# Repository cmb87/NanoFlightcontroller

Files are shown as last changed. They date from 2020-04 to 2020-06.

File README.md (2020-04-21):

# Generic Arduino Based Flightcontroller

## Code
There are two versions:

## MultiWii based FC code
(see https://github.com/multiwii/multiwii-firmware.git for more details). 

### Compass module
Some modifications of the original code were necessary for the compass module (QMC5883L) and are described here:
https://forum.arduino.cc/index.php?topic=556590.0

0.) Navigate to config.h add the line somewhere behind /* I2C magnetometer */:

        #define QMC5883
        
1.) Navigate to sensors.cpp add following somewhere behind the last #endif statement at the magnetometer section:

        // ************************************************************************************************************
        // I2C Compass QMC5883L
        // ************************************************************************************************************
        // I2C adress: 0x0D (7bit)
        // ************************************************************************************************************
        #if defined(QMC5883)

        #define MAG_ADDRESS 0x0D
        #define MAG_DATA_REGISTER 0x00

        //REG CONTROL

        #define MAG_CTRL_REG1 0x09
        #define QMC_MODE 0xC1 // 11 00 00 01OSR=64(11); Range=2G(00); ODR=10Hz(00); MODE=Cont(01)
        #define MAG_CTRL_REG2 0x0A

        void Mag_init() {
          i2c_writeReg(MAG_ADDRESS,0x0B,0x01);
          i2c_writeReg(MAG_ADDRESS,MAG_CTRL_REG1,QMC_MODE);
        }

        static void getADC() {
          i2c_getSixRawADC(MAG_ADDRESS,MAG_DATA_REGISTER);
          MAG_ORIENTATION( ((rawADC[1]<<8) | rawADC[0]) ,
                           ((rawADC[3]<<8) | rawADC[2]) ,
                           ((rawADC[5]<<8) | rawADC[4]) );
        }

        #if !defined(MPU6050_I2C_AUX_MASTER)
        static void Device_Mag_getADC() {
          getADC();
        }
        #endif
        #endif

Now we need to add the QMC to the MPU6050 I2C Master & Slave functionality:

Search for this comment in sensors.cpp:

        //The MAG acquisition function must be replaced because we now talk to the MPU device

Add following lines inside static void Device_Mag_getADC(){} after i2c_getSixRawADC(MPU6050_ADDRESS, 0x49);:

        #if defined(QMC5883)
                MAG_ORIENTATION( ((rawADC[1]<<8) | rawADC[0]) ,
                                 ((rawADC[3]<<8) | rawADC[2]) ,
                                 ((rawADC[5]<<8) | rawADC[4]) );
              #endif
              
Navigate to def.h search for the MAG 1 definition "#if" clause - add "|| defined(QMC5883)" - like this:

        #if defined(HMC5883) || defined(HMC5843) || defined(AK8975) || defined(MAG3110) || defined(QMC5883)
          #define MAG 1
        #else
          #define MAG 0
        #endif
              
The original HMC5883 Code has lots of more lines because of some ominous bias and gain settings - the QMC5883 lacks those registers - Unfortunately I don't have any knowledge about this and its benefits and no time to get into it. The data provided by the sensor seems to be reliable.

### Setup
Due to the construction of the flight controller the following settings were necessary:
            
          MINTHROTTLE = 1150
          # ==============================================
          # MPU Setup 
          # ==============================================
          # Roll and Yaw inverted
          #define ACC_ORIENTATION(X, Y, Z) {imu.accADC[ROLL] =  -X; imu.accADC[PITCH] =  -Y; imu.accADC[YAW] = Z;}
          #define GYRO_ORIENTATION(X, Y, Z) {imu.gyroADC[ROLL] = -X; imu.gyroADC[PITCH] = -Y; imu.gyroADC[YAW] = Z;}
          
          # ==============================================
          # Inverted Pitch ... let's see ===> Not a good idea ... Create oscillations!
          #define ACC_ORIENTATION(X, Y, Z) {imu.accADC[ROLL] =  X; imu.accADC[PITCH] =  Y; imu.accADC[YAW] = -Z;}
          #define GYRO_ORIENTATION(X, Y, Z) {imu.gyroADC[ROLL] = -X; imu.gyroADC[PITCH] = Y; imu.gyroADC[YAW] = -Z;}

          # ==============================================
          WORKING!!!!
          # Roll and Yaw inverted ==> Stabilize around roll axis! Roll appears inverted in MultiwiiConf!!!
          #define ACC_ORIENTATION(X, Y, Z) {imu.accADC[ROLL] =  X; imu.accADC[PITCH] =  -Y; imu.accADC[YAW] = -Z;}
          #define GYRO_ORIENTATION(X, Y, Z) {imu.gyroADC[ROLL] = -X; imu.gyroADC[PITCH] = -Y; imu.gyroADC[YAW] = -Z;}
          # PID Coeff; Roll; 4.1, 0.004,9 Pitch:1.6, 0.003,4 Yaw: 1.6, 0.003, 2
          
          # ==============================================
          # MPU + Compass
          # ==============================================
          WORKING!!!! Works perfectly with 
          #define YAW_DIRECTION -1
          #define ACC_ORIENTATION(X, Y, Z) {imu.accADC[ROLL] =  X; imu.accADC[PITCH] =  -Y; imu.accADC[YAW] = -Z;}
          #define GYRO_ORIENTATION(X, Y, Z) {imu.gyroADC[ROLL] = -X; imu.gyroADC[PITCH] = -Y; imu.gyroADC[YAW] = -Z;}
          #define FORCE_MAG_ORIENTATION(X, Y, Z)  {imu.magADC[ROLL]  =   -X; imu.magADC[PITCH]  =  -Y; imu.magADC[YAW]  = -Z;}

### ESC Calibration
Dont forget the ESC calibration in config.h!

### Custom Arduino based FC code
Inspired by http://www.electronoobs.com

## PCB
Created with Fritzing and Flatcam.

# Issues
Some issues encountered during the construction phase.

## Vibrations
Has a very intensive impact on PID controller resulting in twitches and an in general "nervous" behaviour of the quad. In order to mitigate there are three ways:

    1.) Reduce vibrations by accurately balancing propellers
    2.) Increase damping of the flight controller module
    3.) In MultiWii: Reduce low pass filter to e.g. 42hz for gyro and activate moving average filter (with default settings). Search for LPF in config.h

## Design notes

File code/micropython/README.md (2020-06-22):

https://github.com/tuupola/micropython-mpu9250

# By default the library returns 3-tuple of X, Y, Z axis values for either acceleration, gyroscope and magnetometer ie compass. Default units are m/s^2, rad/s, uT and °C. It is possible to also get acceleration values in g and gyro values deg/s. See the example below. Note that both the MPU6500 and the AK8963 drivers are available as separate classes. MPU9250 is actually a composite of those two.

import utime
from machine import I2C, Pin
from mpu9250 import MPU9250

i2c = I2C(scl=Pin(22), sda=Pin(21))
sensor = MPU9250(i2c)

print("MPU9250 id: " + hex(sensor.whoami))

while True:
    print(sensor.acceleration)
    print(sensor.gyro)
    print(sensor.magnetic)
    print(sensor.temperature)

    utime.sleep_ms(1000)

# More realistic example usage with timer. If you get OSError: 26 or i2c driver install error after soft reboot do a hard reboot.

import utime
from machine import I2C, Pin
from mpu9250 import MPU9250
from mpu6500 import MPU6500, SF_G, SF_DEG_S

i2c = I2C(scl=Pin(22), sda=Pin(21))
mpu6500 = MPU6500(i2c, accel_sf=SF_G, gyro_sf=SF_DEG_S)
sensor = MPU9250(i2c, mpu6500=mpu6500)

print("MPU9250 id: " + hex(sensor.whoami))

while True:
    print(sensor.acceleration)
    print(sensor.gyro)
    print(sensor.magnetic)
    print(sensor.temperature)

    utime.sleep_ms(1000)

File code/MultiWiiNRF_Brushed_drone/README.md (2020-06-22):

/*  From iforced2D, changed by ELECTRONOOBS 02/03/2018
 *  This is the code used for a brushed drone. Motors are conencted to D3, D5, D6 adn D9
 *  NRF24 is connected to D13, D12, D11, D8 and D7
 *  IMU is connected to A4 and A5
 *  Check the tutorial here: http://www.electronoobs.com/eng_arduino_tut23.php
 *  And the video here: https://www.youtube.com/watch?v=uZKINPm3P9E
 *  
 * 
 * Go to NRF24_RX if you want to change CE adn CSN pins and the received bytes
 * Go to config.c to cahnge drone configuration
 * Go to output.cpp to cahnge the output PWM signal
 * 
 * 
 * 
 * 
 * 
 * 
 * 
 * 
 * 
 * Welcome to MultiWii.
 *
 * If you see this message, chances are you are using the Arduino IDE. That is ok.
 * To get the MultiWii program configured for your copter, you must switch to the tab named 'config.h'.
 * Maybe that tab is not visible in the list at the top, then you must use the drop down list at the right
 * to access that tab. In that tab you must enable your baord or sensors and optionally various features.
 * For more info go to http://www.multiwii.com/wiki/index.php?title=Main_Page
 *
 * Have fun, and do not forget MultiWii is made possible and brought to you under the GPL License.
 *
 */

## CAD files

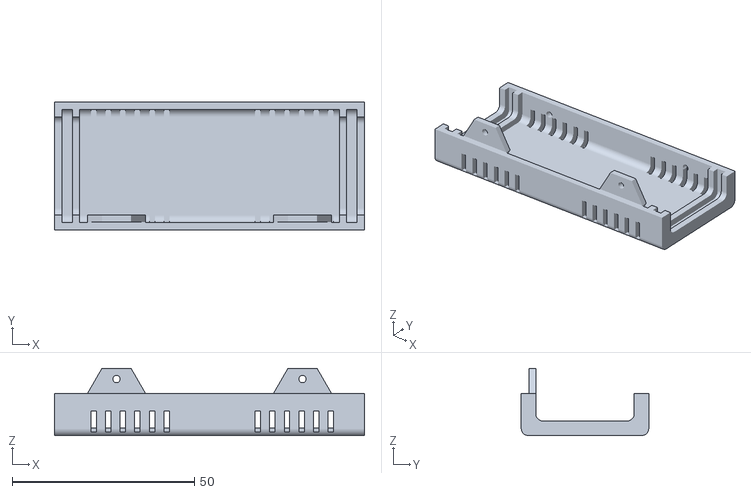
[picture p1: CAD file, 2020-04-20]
casing/bottom.stl
85.0 x 35.0 x 18.4

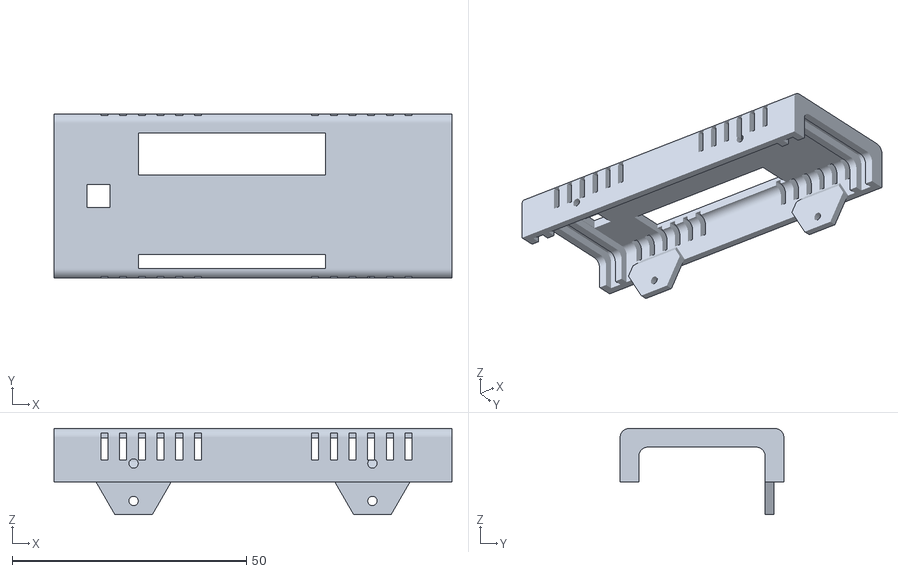
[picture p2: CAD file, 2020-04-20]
casing/top.stl
85.0 x 35.0 x 18.4

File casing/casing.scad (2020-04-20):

/*//////////////////////////////////////////////////////////////////
              -    FB Aka Heartman/Hearty 2016     -                   
              -   http://heartygfx.blogspot.com    -                  
              -       OpenScad Parametric Box      -                     
              -         CC BY-NC 3.0 License       -                      
////////////////////////////////////////////////////////////////////                                                                                                             
12/02/2016 - Fixed minor bug 
28/02/2016 - Added holes ventilation option                    
09/03/2016 - Added PCB feet support, fixed the shell artefact on export mode. 

*/////////////////////////// - Info - //////////////////////////////

// All coordinates are starting as integrated circuit pins.
// From the top view :

//   CoordD           <---       CoordC
//                                 ^
//                                 ^
//                                 ^
//   CoordA           --->       CoordB


////////////////////////////////////////////////////////////////////


////////// - Paramètres de la boite - Box parameters - /////////////

/* [Box dimensions] */
// - Longueur - Length  
  Length        = 75+14-4;       
// - Largeur - Width
  Width         = 31+4;                     
// - Hauteur - Height  
  Height        = 23;  
// - Epaisseur - Wall thickness  
  Thick         = 2;//[2:5]  
  
/* [Box options] */
// Pieds PCB - PCB feet (x4) 
  PCBFeet       = 0;// [0:No, 1:Yes]
// - Decorations to ventilation holes
  Vent          = 1;// [0:No, 1:Yes]
// - Decoration-Holes width (in mm)
  Vent_width    = 1.5;   
// - Text you want
  txt           = "cmb87";           
// - Font size  
  TxtSize       = 3;                 
// - Font  
  Police        ="Arial Black"; 
// - Diamètre Coin arrondi - Filet diameter  
  Filet         = 2;//[0.1:12] 
// - lissage de l'arrondi - Filet smoothness  
  Resolution    = 50;//[1:100] 
// - Tolérance - Tolerance (Panel/rails gap)
  m             = 0.9;
  
/* [PCB_Feet--the_board_will_not_be_exported) ] */
//All dimensions are from the center foot axis
// - Coin bas gauche - Low left corner X position
PCBPosX         = 7;
// - Coin bas gauche - Low left corner Y position
PCBPosY         = 6;
// - Longueur PCB - PCB Length
PCBLength       = 70;
// - Largeur PCB - PCB Width
PCBWidth        = 50;
// - Heuteur pied - Feet height
FootHeight      = 10;
// - Diamètre pied - Foot diameter
FootDia         = 8;
// - Diamètre trou - Hole diameter
FootHole        = 3;  
  

/* [STL element to export] */
//Coque haut - Top shell
  TShell        = 1;// [0:No, 1:Yes]
//Coque bas- Bottom shell
  BShell        = 0;// [0:No, 1:Yes]
//Panneau arrière - Back panel  
  BPanel        = 0;// [0:No, 1:Yes]
//Panneau avant - Front panel
  FPanel        = 0;// [0:No, 1:Yes]
//Texte façade - Front text
  Text          = 0;// [0:No, 1:Yes]


  
/* [Hidden] */
// - Couleur coque - Shell color  
Couleur1        = "Orange";       
// - Couleur panneaux - Panels color    
Couleur2        = "OrangeRed";    
// Thick X 2 - making decorations thicker if it is a vent to make sure they go through shell
Dec_Thick       = Vent ? Thick*2 : Thick; 
// - Depth decoration
Dec_size        = Vent ? Thick*2 : 0.8;

//////////////////// Oversize PCB limitation -Actually disabled - ////////////////////
//PCBL= PCBLength+PCBPosX>Length-(Thick*2+7) ? Length-(Thick*3+20+PCBPosX) : PCBLength;
//PCBW= PCBWidth+PCBPosY>Width-(Thick*2+10) ? Width-(Thick*2+12+PCBPosY) : PCBWidth;
PCBL=PCBLength;
PCBW=PCBWidth;
//echo (" PCBWidth = ",PCBW);

//translate([7,2.5,6])cube([75,30,2]);

/////////// - Boitier générique bord arrondis - Generic Fileted box - //////////

module RoundBox($a=Length, $b=Width, $c=Height){// Cube bords arrondis
                    $fn=Resolution;            
                    translate([0,Filet,Filet]){  
                    minkowski (){                                              
                        cube ([$a-(Length/2),$b-(2*Filet),$c-(2*Filet)], center = false);
                        rotate([0,90,0]){    
                        cylinder(r=Filet,h=Length/2, center = false);
                            } 
                        }
                    }
                }// End of RoundBox Module

      
////////////////////////////////// - Module Coque/Shell - //////////////////////////////////         

module Coque(){//Coque - Shell  
    Thick = Thick*2;  
    difference(){    
        difference(){//sides decoration
            union(){    
                     difference() {//soustraction de la forme centrale - Substraction Fileted box
                      
                        difference(){//soustraction cube median - Median cube slicer
                            union() {//union               
                            difference(){//Coque    
                                RoundBox();
                                translate([Thick/2,Thick/2,Thick/2]){     
                                        RoundBox($a=Length-Thick, $b=Width-Thick, $c=Height-Thick);
                                        }
                                        }//Fin diff Coque                            
                                difference(){//largeur Rails        
                                     translate([Thick+m,Thick/2,Thick/2]){// Rails
                                          RoundBox($a=Length-((2*Thick)+(2*m)), $b=Width-Thick, $c=Height-(Thick*2));
                                                          }//fin Rails
                                     translate([((Thick+m/2)*1.55),Thick/2,Thick/2+0.1]){ // +0.1 added to avoid the artefact
                                          RoundBox($a=Length-((Thick*3)+2*m), $b=Width-Thick, $c=Height-Thick);
                                                    }           
                                                }//Fin largeur Rails
                                    }//Fin union                                   
                               translate([-Thick,-Thick,Height/2]){// Cube à soustraire
                                    cube ([Length+100, Width+100, Height], center=false);
                                            }                                            
                                      }//fin soustraction cube median - End Median cube slicer
                               translate([-Thick/2,Thick,Thick]){// Forme de soustraction centrale 
                                    RoundBox($a=Length+Thick, $b=Width-Thick*2, $c=Height-Thick);       
                                    }                          
                                }                                          


                difference(){// Fixation box legs
                    union(){
                        translate([3*Thick +5,Thick,Height/2]){
                            rotate([90,0,0]){
                                    $fn=6;
                                    cylinder(d=16,Thick/2);
                                    }   
                            }
                            
                       translate([Length-((3*Thick)+5),Thick,Height/2]){
                            rotate([90,0,0]){
                                    $fn=6;
                                    cylinder(d=16,Thick/2);
                                    }   
                            }

                        }
                            translate([4,Thick+Filet,Height/2-57]){   
                             rotate([45,0,0]){
                                   cube([Length,40,40]);    
                                  }
                           }
                           translate([0,-(Thick*1.46),Height/2]){
                                cube([Length,Thick*2,10]);
                           }
                    } //Fin fixation box legs
            }

        union(){// outbox sides decorations
            //if(Thick==1){Thick=2;
            for(i=[0:Thick:Length/4]){

                // Ventilation holes part code submitted by Ettie - Thanks ;) 
                    translate([10+i,-Dec_Thick+Dec_size,1]){
                    cube([Vent_width,Dec_Thick,Height/4]);
                    }
                    translate([(Length-10) - i,-Dec_Thick+Dec_size,1]){
                    cube([Vent_width,Dec_Thick,Height/4]);
                    }
                    translate([(Length-10) - i,Width-Dec_size,1]){
                    cube([Vent_width,Dec_Thick,Height/4]);
                    }
                    translate([10+i,Width-Dec_size,1]){
                    cube([Vent_width,Dec_Thick,Height/4]);
                    }
  
                
                    }// fin de for
               // }
                }//fin union decoration
            }//fin difference decoration
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

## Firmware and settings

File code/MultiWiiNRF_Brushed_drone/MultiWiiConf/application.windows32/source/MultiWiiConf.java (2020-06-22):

import processing.core.*; 
import processing.xml.*; 

import processing.serial.Serial; 
import controlP5.*; 
import processing.opengl.*; 
import java.lang.StringBuffer; 
import javax.swing.SwingUtilities; 
import javax.swing.JFileChooser; 
import javax.swing.filechooser.FileFilter; 
import javax.swing.JOptionPane; 
import java.util.*; 
import java.io.*; 

import java.applet.*; 
import java.awt.Dimension; 
import java.awt.Frame; 
import java.awt.event.MouseEvent; 
import java.awt.event.KeyEvent; 
import java.awt.event.FocusEvent; 
import java.awt.Image; 
import java.io.*; 
import java.net.*; 
import java.text.*; 
import java.util.*; 
import java.util.zip.*; 
import java.util.regex.*; 

public class MultiWiiConf extends PApplet {

 // serial library
 // controlP5 library
 
 // for efficient String concatemation
 // required for swing and EDT
 // Saving dialogue
 // for our configuration file filter "*.mwi"
 // for message dialogue

//Added For  Processing 2.0.x compabillity


//****************************

// TODO add new msp :  pid description with bound and scale

PrintWriter output;
BufferedReader reader;
String portnameFile="SerialPort.txt"; // Name of file for Autoconnect.
int GUI_BaudRate = 115200; // Default.
int SerialPort;
Serial g_serial;
ControlP5 controlP5;
Textlabel txtlblWhichcom,TxtInfoMotors1;
Textlabel txtlblRates,txtlblRev,TxtLeftW,TxtRightW,TxtRevW,TxtRevR,TxtRates,TxtRev,
          TxtMids,TxtMin,TxtMax,TxtSLeft,TxtSNick,TxtSRight,TxtInfo,TxtInfo1,TxtInfo2,
          TxtInfo3,TxtInfo4,TxtAux,Links;

ListBox commListbox,baudListbox;

static int CHECKBOXITEMS=0;
static int PIDITEMS=10;
int commListMax;
int tabHeight=20; // Extra height needed for Tabs
int Centerlimits[]  = {1200,1800}; // Endpoints of ServoCenterSliders 

cGraph g_graph;
int windowsX    = 1000;       int windowsY    = 540+tabHeight;
int xGraph      = 10;         int yGraph      = 325+tabHeight;
int xObj        = 520;        int yObj        = 293+tabHeight;
int xCompass    = 920;        int yCompass    = 341+tabHeight;
int xLevelObj   = 920;        int yLevelObj   = 80+tabHeight; 
int xParam      = 120;        int yParam      = 5+tabHeight;
int xRC         = 690;        int yRC         = 10+tabHeight; 
int xMot        = 690;        int yMot        = 155+tabHeight;
int xButton     = 845;        int yButton     = 231+tabHeight;
int xBox        = 415;        int yBox        = 10+tabHeight;
int xGPS        = 853;        int yGPS        = 438+tabHeight;
int xServ       = 350;        int yServ       = 20+tabHeight; 

int i, j; // enummerators
int byteRC_RATE,byteRC_EXPO, byteRollPitchRate,byteYawRate,
    byteDynThrPID,byteThrottle_EXPO, byteThrottle_MID, byteSelectSetting,
    cycleTime, i2cError,
    version, versionMisMatch,horizonInstrSize,
    GPS_distanceToHome, GPS_directionToHome,
    GPS_numSat, GPS_fix, GPS_update, GPS_altitude, GPS_speed,
    GPS_latitude, GPS_longitude,
    init_com, graph_on, pMeterSum, intPowerTrigger, bytevbat;
    
int multiCapability = 0; // Bitflags stating what capabilities are/are not present in the compiled code.
int byteMP[] = new int[8];  // Motor Pins.  Varies by multiType and Arduino model (pro Mini, Mega, etc).
int MConf[]  = new int[10]; // Min/Maxthro etc
int byteP[] = new int[PIDITEMS], byteI[] = new int[PIDITEMS], byteD[] = new int[PIDITEMS];
int activation[];
int ServoMID[]       = new int[8];  // Plane,ppm/pwm conv,heli
int servoRATE[]      = new int[8];
int servoDirection[] = new int[8];
int ServoMIN[]       = new int[8];
int ServoMAX[]       = new int[8];
int wingDir[]        = new int[8];  // Flying wing
int wingPos[]        = new int[8];
int In[]             = new int[8];

Textlabel TxtMIX[]   = new Textlabel[6];

int multiType;  // 1 for tricopter, 2 for quad+, 3 for quadX, ...
// Alias for multiTypes
int TRI           =1;
int QUADP         =2;
int QUADX         =3;
int BI            =4;
int GIMBAL        =5;
int Y6            =6;
int HEX6          =7;
int FLYING_WING   =8;
int Y4            =9;
int HEX6X         =10;
int OCTOX8        =11;
int OCTOFLATX     =12;
int OCTOFLATP     =13;
int AIRPLANE      =14;
int HELI_120_CCPM =15;
int HELI_90_DEG   =16;
int VTAIL4        =17;
int HEX6H         =18;
int PPM_TO_SERVO  =19;
int DUALCOPTER    =20;
int SINGLECOPTER  =21;


float gx, gy, gz, ax, ay, az, magx, magy, magz, alt, head, angx, angy,
      debug1, debug2, debug3, debug4,
      angyLevelControl, angCalc;

float mot[] = new float[8],
      servo[] = new float[8],
      RCChan[] = new float[16];

private static final int ROLL = 0, PITCH = 1, YAW = 2, ALT = 3, VEL = 4, LEVEL = 5, MAG = 6;

boolean axGraph =true,ayGraph=true,azGraph=true,gxGraph=true,gyGraph=true,gzGraph=true,altGraph=true,headGraph=true, magxGraph =true,magyGraph=true,magzGraph=true,
        debug1Graph = false,debug2Graph = false,debug3Graph = false,debug4Graph = false,hideDraw=false,GraphicsInited=false,gimbalConfig=false,flapperons=false,
        flaps=false,InitServos=true;

boolean toggleServo=false,toggleWriteServo=false,toggleWing=false,toggleWriteWing=false,toggleLive=false,toggleWriteServoLive=false,toggleWriteWingLive=false,
        toggleSaveHeli=false,toggleWaitHeli=false,toggleGimbal=false,
	graphEnabled = false,Mag_=false,gimbal=false, servoStretch=false,camTrigger=false,ExportServo=false,
        toggleTrigger=false,ServosActive=false;

static int RCThro = 3, RCRoll = 0, RCPitch =1, RCYaw =2, RCAUX1=4, RCAUX2=5, RCAUX3=6, RCAUX4=7;

cDataArray accPITCH   = new cDataArray(200), accROLL    = new cDataArray(200), accYAW     = new cDataArray(200),
           gyroPITCH  = new cDataArray(200), gyroROLL   = new cDataArray(200), gyroYAW    = new cDataArray(200),
           magxData   = new cDataArray(200), magyData   = new cDataArray(200), magzData   = new cDataArray(200),
           altData    = new cDataArray(200), headData   = new cDataArray(200),
           debug1Data = new cDataArray(200), debug2Data = new cDataArray(200), debug3Data = new cDataArray(200),
           debug4Data = new cDataArray(200);


Numberbox confP[]   = new Numberbox[PIDITEMS],
          confI[]   = new Numberbox[PIDITEMS],
          confD[]   = new Numberbox[PIDITEMS],
          confINF[] = new Numberbox[7],
          VBat[]    = new Numberbox[6]
          ;

Numberbox confRC_RATE, confRC_EXPO, rollPitchRate, yawRate, dynamic_THR_PID, throttle_EXPO, throttle_MID, 
          confPowerTrigger, confSetting, confSelectSetting;


Slider axSlider, aySlider, azSlider, gxSlider, gySlider, gzSlider, magxSlider, magySlider,
       magzSlider, altSlider, headSlider, debug1Slider, debug2Slider, debug3Slider, debug4Slider,scaleSlider,motorControlSlider;

Slider servoSliderH[]     = new Slider[8],
       servoSliderV[]     = new Slider[8],
       motSlider[]        = new Slider[8],
       TX_StickSlider[]   = new Slider[8],
       GimbalSlider[]     = new Slider[12],
       ServoSliderC[]     = new Slider[8],
       ServoSliderMAX[]   = new Slider[8],
       ServoSliderMIN[]   = new Slider[8];


Button buttonIMPORT, buttonSAVE, buttonREAD, buttonRESET, buttonWRITE, buttonCALIBRATE_ACC, buttonCALIBRATE_MAG, buttonSTART, buttonSTOP, buttonSETTING, 
       buttonAcc, buttonBaro, buttonMag, buttonGPS, buttonSonar, buttonOptic, buttonRXbind, btnQConnect,buttonExport,
       btMagDecl,btMWiiHome,btDownloads;

Button SaveSERVO,buttonSERVO,buttonWing,SaveWing,buttonLIVE,buttonCCPM,buttonGimbal,btnTrigger;

Toggle tACC_ROLL, tACC_PITCH, tACC_Z, tGYRO_ROLL, tGYRO_PITCH, tGYRO_YAW, tBARO,tHEAD, tMAGX, tMAGY, tMAGZ, 
        tDEBUG1, tDEBUG2, tDEBUG3, tDEBUG4;

// Motors Toggles
Toggle motToggle[] = new Toggle[8];

// Colors
int yellow_ = color(200, 200, 20), green_ = color(30, 120, 30), red_ = color(120, 30, 30), blue_ = color(50, 50, 100),
       grey_ = color(30, 30, 30),black_ = color(0, 0, 0),orange_ =color(200,128,0);

PFont font8, font9, font12, font15;

CheckBox checkbox[], checkboxRev[];
CheckBox Bbox,  Wbox,  Mbox;
Button buttonCheckbox[], BtServo[], BtAUX[];
Numberbox RateSlider[];

// TODO New part
public void create_GimbalGraphics(){
  if(gimbal){
  gimbalConfig = true;
  int sMin=1020;int sMax=2000;
  if(servoStretch) {sMin=500; sMax=2500;}
  int Step=yServ-10; 
  GimbalSlider[0] = controlP5.addSlider("Tilt_Min" ,sMin,1500,0,xServ+10,Step+80,60,10)  .setDecimalPrecision(0).hide().moveTo("ServoSettings");
  GimbalSlider[1] = controlP5.addSlider("Tilt_Max" ,1500,sMax,0,xServ+150 ,Step+80,60,10).setDecimalPrecision(0).hide().moveTo("ServoSettings");
  GimbalSlider[2] = controlP5.addSlider("Channel " ,1200,1700,0,xServ+100,Step+60,90,10) .setDecimalPrecision(0).hide().moveTo("ServoSettings");
  GimbalSlider[3] = controlP5.addSlider("Tilt_Prop",-125,125,0,xServ+100,Step+100, 60,10)  .setDecimalPrecision(0).hide().moveTo("ServoSettings");
  Step+=90;
  GimbalSlider[4] = controlP5.addSlider("Roll_Min" ,sMin,1500,0,xServ+10,Step+80,60,10)  .setDecimalPrecision(0).hide().moveTo("ServoSettings");
  GimbalSlider[5] = controlP5.addSlider("Roll_Max" ,1500,sMax,0,xServ+150 ,Step+80,60,10).setDecimalPrecision(0).hide().moveTo("ServoSettings");
  GimbalSlider[6] = controlP5.addSlider("Channel" ,1200,1700,0,xServ+100,Step+60,90,10)  .setDecimalPrecision(0).hide().moveTo("ServoSettings");
  GimbalSlider[7] = controlP5.addSlider("Roll_Prop",-125,125,0,xServ+100,Step+100, 60,10)  .setDecimalPrecision(0).hide().moveTo("ServoSettings");
  
  GimbalSlider[8] = controlP5.addSlider("Trig_LO" ,500,2000,0,xServ+10,Step+80,60,10)   .setDecimalPrecision(0).hide().moveTo("ServoSettings");
  GimbalSlider[9] = controlP5.addSlider("Trig_HI" ,1000,sMax,0,xServ+150 ,Step+80,60,10) .setDecimalPrecision(0).hide().moveTo("ServoSettings");
  GimbalSlider[10] = controlP5.addSlider("Trigger" ,0,30000,0,xServ+100,Step+60,90,10)   .setDecimalPrecision(0).hide().moveTo("ServoSettings");
  GimbalSlider[11] = controlP5.addSlider("Trig_Rev",-0,1,0,xServ+100,Step+100, 40,10)    .setDecimalPrecision(0).hide().moveTo("ServoSettings") .setNumberOfTickMarks(2).setColorTickMark(0);

  buttonGimbal.show();
  if(camTrigger)btnTrigger.show();
  controlP5.getTab("ServoSettings").show();
  }
}
  
public void create_ServoGraphics(){
  BtServo = new Button[8];
  BtAUX   = new Button[5];
  checkboxRev = new CheckBox[8];
  RateSlider = new Numberbox[8];
  GraphicsInited=true;
  Bbox = controlP5.addCheckBox("Bbox").setPosition(xServ+40,yServ+40).setColorForeground(color(120))
                .setColorActive(color(255)).setColorLabel(color(255)).setSize(20, 10).setColorBackground(color(140))
                .setItemsPerRow(1).setSpacingColumn(30).setSpacingRow(10)
                .addItem("0", 254).addItem("1", 254).addItem("2", 254)
                .addItem("3", 254).addItem("4", 254).addItem("5", 254)
                .addItem("6", 254).addItem("7", 254)
                .hide().hideLabels().moveTo("ServoSettings")
                ;
 
 //Create Common ServoSliders
 int Step =0; 
  int sMin=1020;int sMax=2000;
  if(servoStretch) {sMin=500; sMax=2500;}
   for (i=0;i<8;i++) {
     ServoSliderC[i]    =  controlP5.addSlider("Servo "+i,Centerlimits[0],Centerlimits[1],0,xServ+180,yServ+40+Step,110,12).setDecimalPrecision(0).hide().setLabel("").moveTo("ServoSettings");
     ServoSliderMIN[i]  =  controlP5.addSlider("MIN "+i,sMin,1500,0,xServ+80,yServ+40+Step,40,12).setDecimalPrecision(0).setLabel("").hide().moveTo("ServoSettings");
     ServoSliderMAX[i]  =  controlP5.addSlider("MAX "+i,1500,sMax,0,xServ+125,yServ+40+Step,40,12).setDecimalPrecision(0).setLabel("").hide().moveTo("ServoSettings");
     Step+=20; }
	 
 // ServoGraphics For AirPlane SC & DC
if(multiType == PPM_TO_SERVO || multiType == AIRPLANE ){
  controlP5.getTab("ServoSettings").show();
   TxtRates  = controlP5.addTextlabel("label","Servo Rates in %").setPosition(xServ+75,yServ+20).hide().moveTo("ServoSettings");
   TxtMids   = controlP5.addTextlabel("Mlabel","Offset for servos").setPosition(xServ+190,yServ+20).hide().moveTo("ServoSettings");
   TxtAux   = controlP5.addTextlabel("Alabel","Channel for Flaps").setPosition(xServ-120,yServ+20).hide().moveTo("ServoSettings");
   TxtRev    = controlP5.addTextlabel("txtlblRev","Norm/Rev").setPosition(xServ+10,yServ+20).hide().moveTo("ServoSettings");
 
//****************** End of AirPlane ********************
}

if(multiType == FLYING_WING || multiType == TRI || multiType == BI  || multiType == DUALCOPTER || multiType == SINGLECOPTER){ //ServoGraphics For FlyingWng & TRI & BI || multiType == DUALCOPTER
controlP5.getTab("ServoSettings").show();
int LabelPos=100;
 
if(multiType == FLYING_WING){
  Wbox = controlP5.addCheckBox("Wbox").setColorForeground(color(120)).setColorBackground(color(140)).setColorActive(color(255)).setColorLabel(color(255)).setSize(20, 10)
       .setItemsPerRow(2).setSpacingColumn(50).setSpacingRow(10).setPosition(xServ-160  ,yServ+50)
       .addItem("L Roll", 254).addItem("R Roll", 254).addItem("L NICK", 254).addItem("R NICK", 254).moveTo("ServoSettings") ;
   TxtLeftW  = controlP5.addTextlabel("Label","Left Wing"  ).setPosition(xServ+110,yServ+40).hide().moveTo("ServoSettings");
   TxtRightW = controlP5.addTextlabel("Rlabel","Right Wing").setPosition(xServ+110,yServ+130).hide().moveTo("ServoSettings");
 }
 if(multiType == TRI){
   Wbox = controlP5.addCheckBox("Wbox").setColorForeground(color(120)).setColorBackground(color(140)).setColorActive(color(255)).setColorLabel(color(255)).setSize(20, 10)
       .setItemsPerRow(1).setSpacingColumn(50).setSpacingRow(10).setPosition(xServ-160  ,yServ+50)
       .addItem("YAW", 254).moveTo("ServoSettings") ;
    TxtLeftW  = controlP5.addTextlabel("Label","Yaw Servo"  ).setPosition(xServ+110,yServ+40).hide().moveTo("ServoSettings");
    TxtRightW = controlP5.addTextlabel("Rlabel"," ").setPosition(xServ+110,yServ+140).hide().moveTo("ServoSettings");    
  }
  if(multiType == BI){
  Wbox = controlP5.addCheckBox("Wbox").setColorForeground(color(120)).setColorBackground(color(140)).setColorActive(color(255)).setColorLabel(color(255)).setSize(20, 10)
       .setItemsPerRow(2).setSpacingColumn(50).setSpacingRow(10).setPosition(xServ-160  ,yServ+50)
       .addItem("L Yaw", 254).addItem("R Yaw", 254).addItem("L NICK", 254).addItem("R NICK", 254).moveTo("ServoSettings") ;
   TxtLeftW  = controlP5.addTextlabel("Label","Left Servo"  ).setPosition(xServ+110,yServ+40).hide().moveTo("ServoSettings");
   TxtRightW = controlP5.addTextlabel("Rlabel","Right Servo").setPosition(xServ+110,yServ+140).hide().moveTo("ServoSettings");
 }
 if(multiType == DUALCOPTER){
  Wbox = controlP5.addCheckBox("Wbox").setColorForeground(color(120)).setColorBackground(color(140)).setColorActive(color(255)).setColorLabel(color(255)).setSize(20, 10)
       .setItemsPerRow(2).setSpacingColumn(70).setSpacingRow(10).setPosition(xServ-160  ,yServ+50)
       .addItem("Pitch ", 254).addItem("Roll ", 254).moveTo("ServoSettings").hide();
   TxtLeftW  = controlP5.addTextlabel("Label","Roll"  ).setPosition(xServ+110,yServ+40).hide().moveTo("ServoSettings");
   TxtRightW = controlP5.addTextlabel("Rlabel","Nick").setPosition(xServ+110,yServ+130).hide().moveTo("ServoSettings");
 }
 if(multiType == SINGLECOPTER){
  Wbox = controlP5.addCheckBox("Wbox").setColorForeground(color(120)).setColorBackground(color(140)).setColorActive(color(255)).setColorLabel(color(255)).setSize(20, 10)
       .setItemsPerRow(2).setSpacingColumn(50).setSpacingRow(10).setPosition(xServ-80  ,yServ+100)
       .addItem(" Right ", 254).addItem("R yaw", 254)
       .addItem(" Left ", 254) .addItem("L yaw", 254)
       .addItem(" Front", 254) .addItem("F yaw", 254)
       .addItem(" Rear", 254)  .addItem("  yaw", 254)
       .moveTo("ServoSettings") ;
LabelPos=60;
 TxtMin    = controlP5.addTextlabel("Minlabel","MIN").setPosition(xServ+85,yServ+80) .hide().moveTo("ServoSettings");
 TxtMax    = controlP5.addTextlabel("Maxlabel","MAX").setPosition(xServ+130,yServ+80).hide().moveTo("ServoSettings");
 TxtMids   = controlP5.addTextlabel("Mlabel","Offset servos").setPosition(xServ+190,yServ+80).hide().moveTo("ServoSettings");
 }

   TxtRevW   = controlP5.addTextlabel("Revlabel","Change Gyro/Acc Direction"  ).setPosition(xServ-165,yServ+30).hide().moveTo("ServoSettings"); 
   TxtRevR   = controlP5.addTextlabel("Revtx","Change Dir in TX To Match"  ).setPosition(xServ-170,yServ+LabelPos).hide().moveTo("ServoSettings"); 

//****************** End of FlyingWng & TRI ********************
}

// ServoGraphics For Heli 120 && 90
if(multiType == HELI_120_CCPM || multiType == HELI_90_DEG ){
controlP5.getTab("ServoSettings").show();
 TxtMin    = controlP5.addTextlabel("Minlabel","MIN").setPosition(xServ+85,yServ+20) .hide().moveTo("ServoSettings");
 TxtMax    = controlP5.addTextlabel("Maxlabel","MAX").setPosition(xServ+130,yServ+20).hide().moveTo("ServoSettings");
 TxtMids   = controlP5.addTextlabel("Mlabel","Offset servos").setPosition(xServ+190,yServ+20).hide().moveTo("ServoSettings");
 TxtRates  = controlP5.addTextlabel("label","Not Used").setPosition(xServ+75,yServ+20).hide().moveTo("ServoSettings");
 TxtRev    = controlP5.addTextlabel("txtlblRev","Servos").setPosition(xServ+10,yServ+20).hide().moveTo("ServoSettings");
 
// CCPM settings
 // Mixer Boxes
 int XPos=xServ+40;
 int YPos=yServ-0; 
 Mbox  = controlP5.addCheckBox("Wbox").setColorForeground(color(120)).setColorBackground(color(140)).setColorActive(color(255)).setColorLabel(color(255)).setSize(20, 10)
       .setItemsPerRow(3).setSpacingColumn(15).setSpacingRow(10).setPosition(XPos-180  ,YPos+50)
       .addItem("mix3_4", 254) .addItem("mix3_2", 254).addItem("mix3_1", 254)
       .addItem("mix4_4", 254) .addItem("mix4_2", 254).addItem("mix4_1", 254)
       .addItem("mix6_4", 254) .addItem("mix6_2", 254).addItem("mix6_1", 254)
       .moveTo("ServoSettings").hideLabels().hide();
 TxtMIX[0]   = controlP5.addTextlabel("mix1","NICK") .setPosition(XPos-220,YPos+50).moveTo("ServoSettings");
 TxtMIX[1]   = controlP5.addTextlabel("mix2","LEFT") .setPosition(XPos-220,YPos+70).moveTo("ServoSettings");
 TxtMIX[2]   = controlP5.addTextlabel("mix3","RIGHT").setPosition(XPos-220,YPos+90).moveTo("ServoSettings"); 
 TxtMIX[3]   = controlP5.addTextlabel("mix4","COLL") .setPosition(XPos-195,YPos+30).moveTo("ServoSettings");
 TxtMIX[4]   = controlP5.addTextlabel("mix5","NICK") .setPosition(XPos-155,YPos+30).moveTo("ServoSettings");
 TxtMIX[5]   = controlP5.addTextlabel("mix6","ROLL") .setPosition(XPos-115,YPos+30).moveTo("ServoSettings");
 for (i=0;i<6;i++) { TxtMIX[i].hide();}

  //******************End of Heli********************
}
// Common Graphics for servos
  Step =0;
  for (i=0;i<8;i++) { // TODO Something
   BtServo[i] = controlP5.addButton("CHb"+i,1,xServ-30,yServ+40+20*i,60,12).setColorBackground(green_).setLabel("Servo "+i).hide().moveTo("ServoSettings");
    
    checkboxRev[i] =  controlP5.addCheckBox("cbR"+i).moveTo("ServoSettings");
    checkboxRev[i].setPosition(xServ+70,yServ+40+20*i)
    .setColorActive(color(255)).setColorBackground(color(120))
    .setItemHeight(10).setItemWidth(20).hide()
    .moveTo("ServoSettings")
    ;
   
    RateSlider[i] = (controlP5.Numberbox) hideLabel(controlP5.addNumberbox("Rate"+i,0,xServ+70,yServ+40+i*20,100,14));
    RateSlider[i].setColorBackground(yellow_);RateSlider[i].setDirection(Controller.HORIZONTAL);
    RateSlider[i].setDecimalPrecision(0);RateSlider[i].setMultiplier(1);RateSlider[i].setMin(0).setMax(125).hide().moveTo("ServoSettings");
  }
  
  for (i=0;i<4;i++) BtAUX[i] = controlP5.addButton("Cau"+i,1,xServ-100,yServ+40+20*i,60,12).setColorBackground(red_).setLabel("  AUX "+(i+1)).moveTo("ServoSettings").hide();
  BtAUX[4] = controlP5.addButton("Cau4" ,1,xServ-100,yServ+120,60,12).setColorBackground(blue_).setLabel("Disable").moveTo("ServoSettings").hide();
  
 //************************ End of servoGrapics********************** 
}

public void create_checkboxes(String[] names) {
  /* destroy old buttons */
  for (int i=0; i<CHECKBOXITEMS; i++) {
    buttonCheckbox[i].remove();
    checkbox[i].remove();
  }
  int i=0;
  /* create new list entries and buttons */
  checkbox = new CheckBox[names.length];
  buttonCheckbox = new Button[names.length];
  activation = new int[names.length];
  for (String name : names) {
  if ( name.equals("CAMTRIG")) camTrigger=true;
  if ( name.equals("CAMSTAB") || name.equals("CAMTRIG")) gimbal=true;
    buttonCheckbox[i] = controlP5.addButton("bcb"+i,1,xBox-30,yBox+20+13*i,68,12).setColorBackground(red_).setLabel(name);
    checkbox[i] =  controlP5.addCheckBox("cb"+i,xBox+40,yBox+20+13*i).setColorActive(color(255)).setColorBackground(color(120)).
    setItemsPerRow(12).setSpacingColumn(10).setLabel("");
    for (int j=1; j<=12; j++) checkbox[i].addItem(i + "_cb_" + j, j).hideLabels();
    i++;
  }
  CHECKBOXITEMS = names.length;
}

// coded by Eberhard Rensch
// Truncates a long port name for better (readable) display in the GUI
public String shortifyPortName(String portName, int maxlen)  {
  String shortName = portName;
  if(shortName.startsWith("/dev/cu.")) shortName = "";// only collect the corresponding tty. devices
  return shortName;
  /*
  if(shortName.startsWith("/dev/")) shortName = shortName.substring(5);  
  if(shortName.startsWith("tty.")) shortName = shortName.substring(4); // get rid of leading tty. part of device name
  if(portName.length()>maxlen) shortName = shortName.substring(0,(maxlen-1)/2) + "~" +shortName.substring(shortName.length()-(maxlen-(maxlen-1)/2));
  if(shortName.startsWith("cu.")) shortName = "";// only collect the corresponding tty. devices
  return shortName;
 */
}

public controlP5.Controller hideLabel(controlP5.Controller c) {
  c.setLabel("");
  c.setLabelVisible(false);
  return c;
}
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
  static public void main(String args[]) {
    PApplet.main(new String[] { "--bgcolor=#ECE9D8", "MultiWiiConf" });
  }
}

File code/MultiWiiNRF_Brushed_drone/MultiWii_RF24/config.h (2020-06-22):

#ifndef CONFIG_H_
#define CONFIG_H_

/*************************************************************************************************/
/****           CONFIGURABLE PARAMETERS                                                       ****/
/*************************************************************************************************/

/* this file consists of several sections
 * to create a working combination you must at least make your choices in section 1.
 * 1 - BASIC SETUP - you must select an option in every block.
 *      this assumes you have 4 channels connected to your board with standard ESCs and servos.
 * 2 - COPTER TYPE SPECIFIC OPTIONS - you likely want to check for options for your copter type
 * 3 - RC SYSTEM SETUP
 * 4 - ALTERNATE CPUs & BOARDS - if you have
 * 5 - ALTERNATE SETUP - select alternate RX (SBUS, PPM, etc.), alternate ESC-range, etc. here
 * 6 - OPTIONAL FEATURES - enable nice to have features here (FlightModes, LCD, telemetry, battery monitor etc.)
 * 7 - TUNING & DEVELOPER - if you know what you are doing; you have been warned
 *     - (ESCs calibration, Dynamic Motor/Prop Balancing, Diagnostics,Memory savings.....)
 * 8 - DEPRECATED - these features will be removed in some future release
 */

/* Notes:
 * 1. parameters marked with (*) in the comment are stored in eeprom and can be changed via serial monitor or LCD.
 * 2. parameters marked with (**) in the comment are stored in eeprom and can be changed via the GUI
 */


/*************************************************************************************************/
/*****************                                                                 ***************/
/****************  SECTION  1 - BASIC SETUP                                                *******/
/*****************                                                                 ***************/
/*************************************************************************************************/

  /**************************    The type of multicopter    ****************************/
    //#define GIMBAL
    //#define BI
    //#define TRI
    //#define QUADP
    #define QUADX
    //#define Y4
    //#define Y6
    //#define HEX6
    //#define HEX6X
    //#define HEX6H  // New Model
    //#define OCTOX8
    //#define OCTOFLATP
    //#define OCTOFLATX
    //#define FLYING_WING
    //#define VTAIL4
    //#define AIRPLANE
    //#define SINGLECOPTER
    //#define DUALCOPTER
    //#define HELI_120_CCPM
    //#define HELI_90_DEG

  /****************************    Motor minthrottle    *******************************/
    /* Set the minimum throttle command sent to the ESC (Electronic Speed Controller)
       This is the minimum value that allow motors to run at a idle speed  */
    //#define MINTHROTTLE 1300 // for Turnigy Plush ESCs 10A
    //#define MINTHROTTLE 1120 // for Super Simple ESCs 10A
    //#define MINTHROTTLE 1064 // special ESC (simonk)
    //#define MINTHROTTLE 1050 // for brushed ESCs like ladybird
    #define MINTHROTTLE 1000 // (*) (**)

  /****************************    Motor maxthrottle    *******************************/
    /* this is the maximum value for the ESCs at full power, this value can be increased up to 2000 */
    #define MAXTHROTTLE 2000

  /****************************    Mincommand          *******************************/
    /* this is the value for the ESCs when they are not armed
       in some cases, this value must be lowered down to 900 for some specific ESCs, otherwise they failed to initiate */
    #define MINCOMMAND  1000

  /**********************************  I2C speed for old WMP config (useless config for other sensors)  *************/
    #define I2C_SPEED 100000L     //100kHz normal mode, this value must be used for a genuine WMP
    //#define I2C_SPEED 400000L   //400kHz fast mode, it works only with some WMP clones

  /***************************    Internal i2c Pullups   ********************************/
    /* enable internal I2C pull ups (in most cases it is better to use external pullups) */
    //#define INTERNAL_I2C_PULLUPS

  /**********************************  constant loop time  ******************************/
    #define LOOP_TIME 2800

  /**************************************************************************************/
  /*****************          boards and sensor definitions            ******************/
  /**************************************************************************************/
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

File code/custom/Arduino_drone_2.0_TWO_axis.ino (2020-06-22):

/* http://www.youtube.com/c/electronoobs
 * 
 * This is an example where we control two axis drone with PID 
 * and data from the radio receiver and the MPU6050 module
 * 
 * Arduino pin    |   MPU6050
 * 5V             |   Vcc
 * GND            |   GND
 * A4             |   SDA
 * A5             |   SCL
 * 
 * F_ Left__motor |   D4
 * F_ Right__motor|   D7
 * B_Left__motor  |   D5
 * B_Right__motor |   D6
  */
#include <Wire.h>
#include <Servo.h>

Servo L_F_prop;
Servo L_B_prop;
Servo R_F_prop;
Servo R_B_prop;


//We create variables for the time width values of each PWM input signal
unsigned long counter_1, counter_2, counter_3, counter_4, current_count;

//We create 4 variables to stopre the previous value of the input signal (if LOW or HIGH)
byte last_CH1_state, last_CH2_state, last_CH3_state, last_CH4_state;

//To store the 1000us to 2000us value we create variables and store each channel
int input_YAW;      //In my case channel 4 of the receiver and pin D12 of arduino
int input_PITCH;    //In my case channel 2 of the receiver and pin D9 of arduino
int input_ROLL;     //In my case channel 1 of the receiver and pin D8 of arduino
int input_THROTTLE; //In my case channel 3 of the receiver and pin D10 of arduino




/*MPU-6050 gives you 16 bits data so you have to create some float constants
*to store the data for accelerations and gyro*/

//Gyro Variables
float elapsedTime, time, timePrev;        //Variables for time control
int gyro_error=0;                         //We use this variable to only calculate once the gyro data error
float Gyr_rawX, Gyr_rawY, Gyr_rawZ;       //Here we store the raw data read 
float Gyro_angle_x, Gyro_angle_y;         //Here we store the angle value obtained with Gyro data
float Gyro_raw_error_x, Gyro_raw_error_y; //Here we store the initial gyro data error

//Acc Variables
int acc_error=0;                            //We use this variable to only calculate once the Acc data error
float rad_to_deg = 180/3.141592654;         //This value is for pasing from radians to degrees values
float Acc_rawX, Acc_rawY, Acc_rawZ;         //Here we store the raw data read 
float Acc_angle_x, Acc_angle_y;             //Here we store the angle value obtained with Acc data
float Acc_angle_error_x, Acc_angle_error_y; //Here we store the initial Acc data error

float Total_angle_x, Total_angle_y;

//More variables for the code
int i;
int mot_activated=0;
long activate_count=0;
long des_activate_count=0;

//////////////////////////////PID FOR ROLL///////////////////////////
float roll_PID, pwm_L_F, pwm_L_B, pwm_R_F, pwm_R_B, roll_error, roll_previous_error;
float roll_pid_p=0;
float roll_pid_i=0;
float roll_pid_d=0;
///////////////////////////////ROLL PID CONSTANTS////////////////////
double roll_kp=0.7;//3.55
double roll_ki=0.006;//0.003
double roll_kd=1.2;//2.05
float roll_desired_angle = 0;     //This is the angle in which we whant the

//////////////////////////////PID FOR PITCH//////////////////////////
float pitch_PID, pitch_error, pitch_previous_error;
float pitch_pid_p=0;
float pitch_pid_i=0;
float pitch_pid_d=0;
///////////////////////////////PITCH PID CONSTANTS///////////////////
double pitch_kp=0.72;//3.55
double pitch_ki=0.006;//0.003
double pitch_kd=1.22;//2.05
float pitch_desired_angle = 0;     //This is the angle in which we whant the

                              

void setup() {
    
  PCICR |= (1 << PCIE0);    //enable PCMSK0 scan                                                 
  PCMSK0 |= (1 << PCINT0);  //Set pin D8 trigger an interrupt on state change. 
  PCMSK0 |= (1 << PCINT1);  //Set pin D9 trigger an interrupt on state change.                                             
  PCMSK0 |= (1 << PCINT2);  //Set pin D10 trigger an interrupt on state change.                                               
  PCMSK0 |= (1 << PCINT4);  //Set pin D12 trigger an interrupt on state change.  

  
  DDRB |= B00100000;  //D13 as output
  PORTB &= B11011111; //D13 set to LOW

  L_F_prop.attach(4); //left front motor
  L_B_prop.attach(5); //left back motor
  R_F_prop.attach(7); //right front motor 
  R_B_prop.attach(6); //right back motor 
  /*in order to make sure that the ESCs won't enter into config mode
  *I send a 1000us pulse to each ESC.*/
  L_F_prop.writeMicroseconds(1000); 
  L_B_prop.writeMicroseconds(1000);
  R_F_prop.writeMicroseconds(1000); 
  R_B_prop.writeMicroseconds(1000);
  
  
  Wire.begin();                           //begin the wire comunication
  Wire.beginTransmission(0x68);           //begin, Send the slave adress (in this case 68)              
  Wire.write(0x6B);                       //make the reset (place a 0 into the 6B register)
  Wire.write(0x00);
  Wire.endTransmission(true);             //end the transmission
  
  Wire.beginTransmission(0x68);           //begin, Send the slave adress (in this case 68) 
  Wire.write(0x1B);                       //We want to write to the GYRO_CONFIG register (1B hex)
  Wire.write(0x10);                       //Set the register bits as 00010000 (100dps full scale)
  Wire.endTransmission(true);             //End the transmission with the gyro

  Wire.beginTransmission(0x68);           //Start communication with the address found during search.
  Wire.write(0x1C);                       //We want to write to the ACCEL_CONFIG register (1A hex)
  Wire.write(0x10);                       //Set the register bits as 00010000 (+/- 8g full scale range)
  Wire.endTransmission(true);  
  
  Serial.begin(9600);
  delay(1000);
  time = millis();                         //Start counting time in milliseconds
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

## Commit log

2020-04-03 first working version
    [config.h, controller.fzz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]
2020-04-20 updated multiwii
    [bottom.stl, casing.scad, config.h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]
2020-04-21 activated moving average filter for gyro and reduce LPF to 42hz
    [config.h]
2020-06-22 last commit
    [config.h, fcV2Nrf.fzz, fcV2Nrf_esc.fzz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]
